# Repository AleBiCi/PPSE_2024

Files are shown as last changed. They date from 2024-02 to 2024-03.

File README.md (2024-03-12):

# PPSE_2024 - SunScanner
Questa repository contiene i file di progetto per l'attività di laboratorio del corso di **Progettazione e Prototipazione di Sistemi Elettronici**.\
Il nostro team ha sviluppato un sistema, denominato **SunScanner**, che tramite dati di geolocalizzazione e lettura della tensione riesce a orientare un pannello fotovoltaico verso il sole con un buon livello di precisione.\
Di seguito vengono elencati i contenuti della repo:
* Nella cartella `SW` è contenuto il progetto PlatformIO per la programmazione della scheda;
* Nella cartella `HW` sono presenti tutti i modelli 3D sviluppati per questo progetto (ed eventualmente pronti per la stampa);
* Nella `DOCUMENTAZIONE` si trova tutto il materiale informativo/le informazioni tecniche utilizzate, compresa la relazione finale.

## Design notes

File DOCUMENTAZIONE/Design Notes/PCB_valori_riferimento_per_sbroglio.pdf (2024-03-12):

Serigrafia

Ref. Componenti -> Tratto 0.16/0.20mm Lettere 0.9/1mm

Descrizioni -> Tratto 0.25 Lettere 1.25mm

Piste rame

Segnale -> 0.2 (minimo 0.127)

Alimentazione 0.5 / 0.75mm

Via

Segnale diametro 0.5mm foro 0.3mm

Alimentazione diametro 1.2mm foro 0.6mm O anche meno

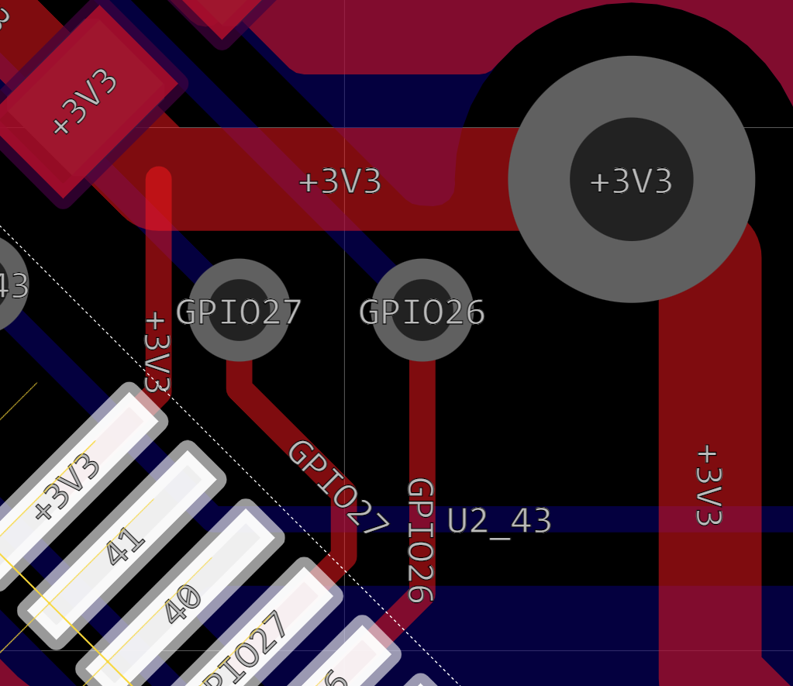
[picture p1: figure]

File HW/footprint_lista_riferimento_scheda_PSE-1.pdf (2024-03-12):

Value | Footprint | Note
Buzzer | Buzzer_Beeper:Buzzer_12x9.5RM7.6
100n | Capacitor_SMD:C_0603_1608Metric
2.2u | Capacitor_SMD:C_0603_1608Metric
18p | Capacitor_SMD:C_0603_1608Metric
4.7u | Capacitor_SMD:C_0603_1608Metric
10u | Capacitor_SMD:C_0805_2012Metric
1u | Capacitor_SMD:C_0603_1608Metric
22u | Capacitor_SMD:C_0805_2012Metric
4u7 | Capacitor_SMD:C_0603_1608Metric
1u 6V3 | Capacitor_SMD:C_0603_1608Metric
WS2812B | LED_SMD:LED_WS2812B_PLCC4_5.0x5.0mm_P3.2mm
1N4148 | Diode_SMD:D_SOD-123
LED_alive | LED_SMD:LED_0603_1608Metric
TVS VBR 17V IBR=1mA | Diode_SMD:D_SMA
S1B | Diode_SMD:D_SMA
RBR1VWM30ATFTR | Diode_SMD:D_SOD-123
3V3_LED | LED_SMD:LED_0805_2012Metric
PDZ3.3B.115 | Diode_SMD:D_SOD-323_HandSoldering
5V_LED | LED_SMD:LED_0805_2012Metric
2016L05MR | Fuse:Fuse_1206_3216Metric
FerriteBead | Capacitor_SMD:C_0805_2012Metric
MountingHole | MountingHole:MountingHole_3.2mm_M3_Pad_Via
WS2812B | Connector_JST:JST_XH_B3B-XH-A_1x03_P2.50mm_Vertical
Conn_01x03 | Connector_PinHeader_2.54mm:PinHeader_1x03_P2.54mm_Vertical
Vin | TerminalBlock:TerminalBlock_bornier-2_P5.08mm
USB_B_Mini | Connector_USB:USB_Mini-B_Wuerth_65100516121_Horizontal
Vout 5V | TerminalBlock:TerminalBlock_bornier-2_P5.08mm
I2C_3V3 | Connector_JST:JST_XH_B4B-XH-A_1x04_P2.50mm_Vertical
UART0_3V3 | Connector_JST:JST_XH_B4B-XH-A_1x04_P2.50mm_Vertical
IRLML0060TRPBF | Package_TO_SOT_SMD:SOT-23
PDTC114YT | Package_TO_SOT_SMD:SOT-23
IRLML9301 | Package_TO_SOT_SMD:SOT-23
1k | Resistor_SMD:R_0603_1608Metric
100k | Resistor_SMD:R_0603_1608Metric
10K | Resistor_SMD:R_0603_1608Metric
10k | Resistor_SMD:R_0603_1608Metric
470k | Resistor_SMD:R_0603_1608Metric
470 | Resistor_SMD:R_0603_1608Metric
27 | Resistor_SMD:R_0603_1608Metric
510 | Resistor_SMD:R_0603_1608Metric
1.8k | Resistor_SMD:R_0603_1608Metric
200 | Resistor_SMD:R_0603_1608Metric
150k | Resistor_SMD:R_0603_1608Metric
56k | Resistor_SMD:R_0603_1608Metric
4.7k | Resistor_SMD:R_0603_1608Metric
47k | Resistor_SMD:R_0603_1608Metric
RESET_SW | Button_Switch_SMD:SW_SPST_EVQP0
PROG_SW | Button_Switch_SMD:SW_SPST_EVQP0
SW_U | Button_Switch_SMD:SW_SPST_EVQP0
SW_L | Button_Switch_SMD:SW_SPST_EVQP0
SW_R | Button_Switch_SMD:SW_SPST_EVQP0
SW_D | Button_Switch_SMD:SW_SPST_EVQP0
Power_button | Button_Switch_SMD:SW_SPST_EVQP0
VBUS | TestPoint:TestPoint_THTPad_D1.5mm_Drill0.7mm
5V | TestPoint:TestPoint_THTPad_D1.5mm_Drill0.7mm
3V3 | TestPoint:TestPoint_THTPad_D1.5mm_Drill0.7mm
3V3A | TestPoint:TestPoint_THTPad_D1.5mm_Drill0.7mm
RP2040 | DA REALIZZARE | Verificare online se esistono footprint di partenza o già disponibili
W25Q16JVUSSQ | DA REALIZZARE | Verificare online se esistono footprint di partenza o già disponibili
AT24C256 | Package_SO:SOIC-8_3.9x4.9mm_P1.27mm
oled_0.96"_128x64px | Connector_PinHeader_2,54mm:PinHeader_1x04_P2.54mm_Vertical | Tenere conto dell'ingombro reale del componente
XC6705A331MR-G | Package_TO_SOT_SMD:SOT-23-5
TPS563201 | Package_TO_SOT_SMD:SOT-23-6
SAM-M8Q | DA REALIZZARE | Verificare online se esistono footprint di partenza o già disponibili
MMA8451Q | DA REALIZZARE | Verificare online se esistono footprint di partenza o già disponibili
ESP-01 | Connector_PinSocket_2,54mm:PinSocket_2x04_P2.54mm_Vertical | Tenere conto dell'ingombro reale del componente
TC1047A | Package_TO_SOT_SMD:SOT-23
12MHz | Crystal:Crystal_SMD_3225-4Pin_3.2x2.5mm_HandSoldering
Induttore 2,2uH | Inductor_SMD:L_Vishay_IHLP-1212 | IHLP1212BZER2R2M11

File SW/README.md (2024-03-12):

## Nota Importante
È possibile aprire e visualizzare correttamente il progetto (completo di dipendenze) solamente utilizzando **PlatformIO**.\
Se si fosse interessati solamente ai file sorgente, nella cartella `src` si trovano i file `.cpp` mentre nella cartella `include` gli header.

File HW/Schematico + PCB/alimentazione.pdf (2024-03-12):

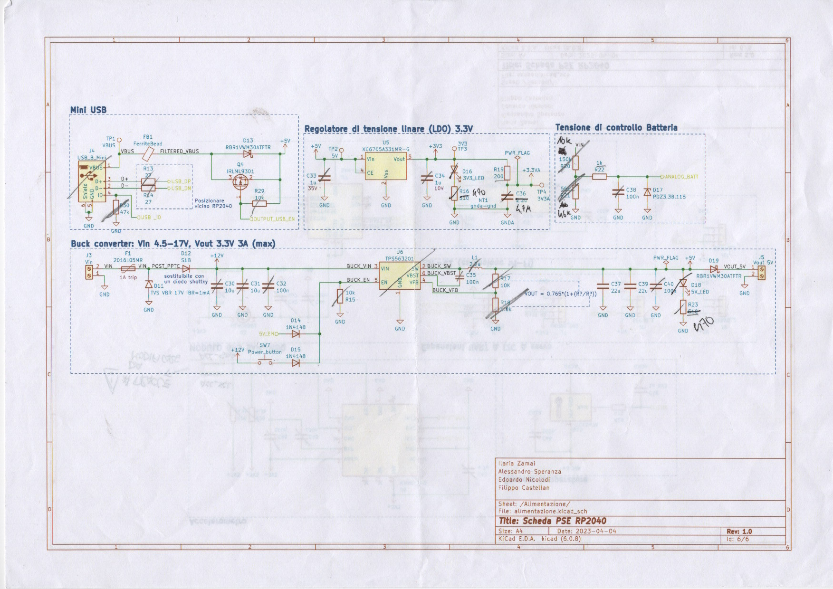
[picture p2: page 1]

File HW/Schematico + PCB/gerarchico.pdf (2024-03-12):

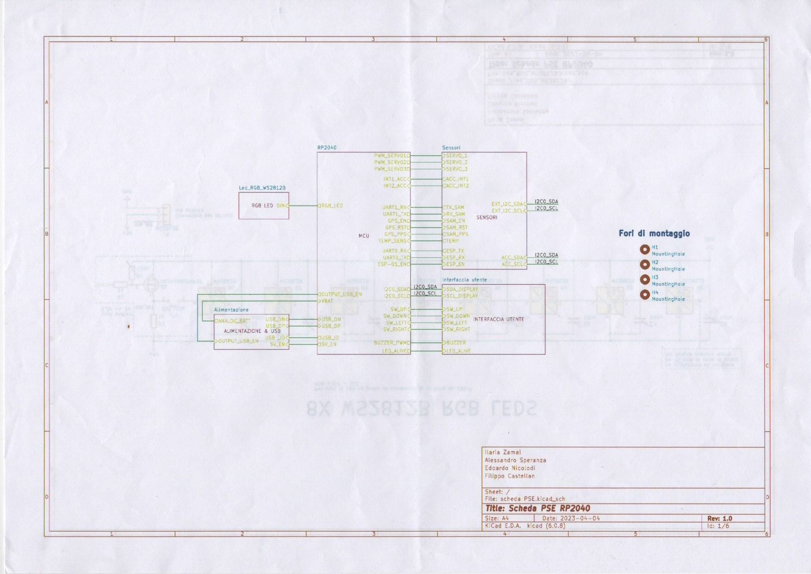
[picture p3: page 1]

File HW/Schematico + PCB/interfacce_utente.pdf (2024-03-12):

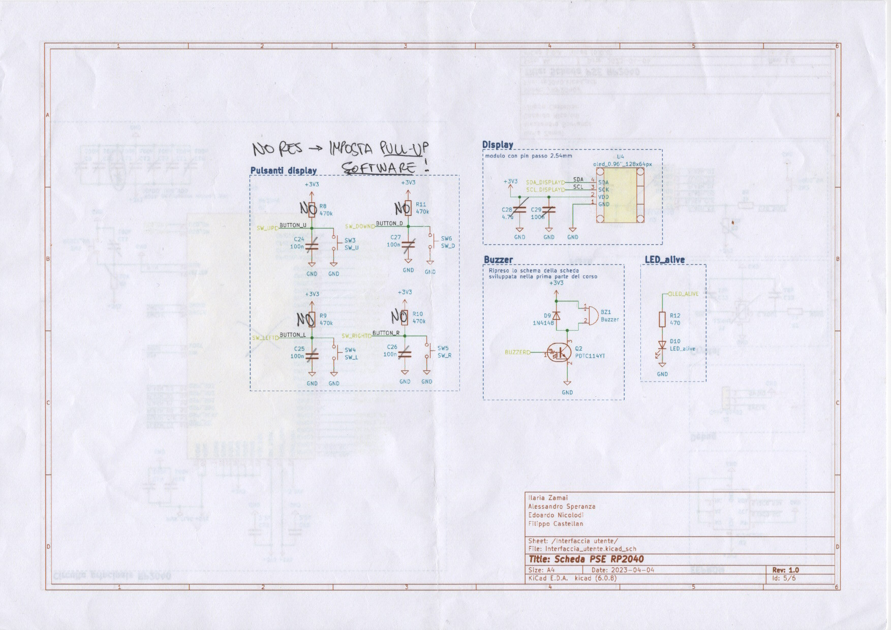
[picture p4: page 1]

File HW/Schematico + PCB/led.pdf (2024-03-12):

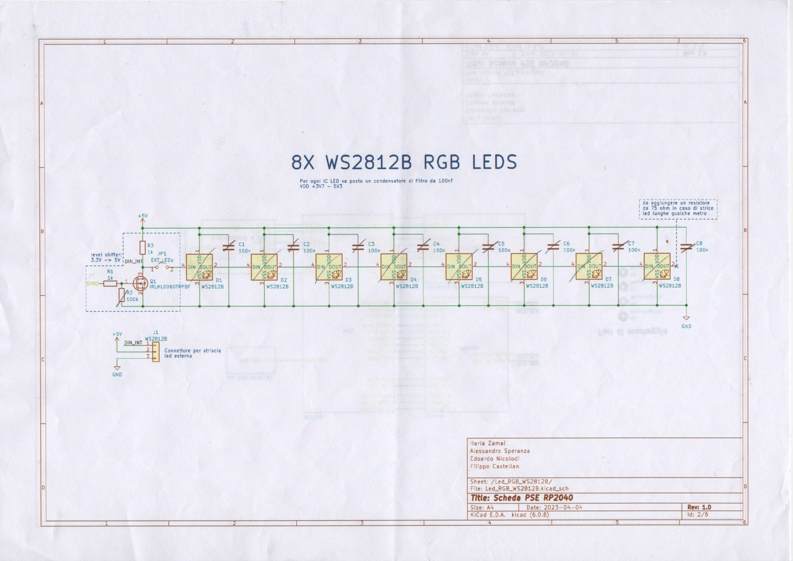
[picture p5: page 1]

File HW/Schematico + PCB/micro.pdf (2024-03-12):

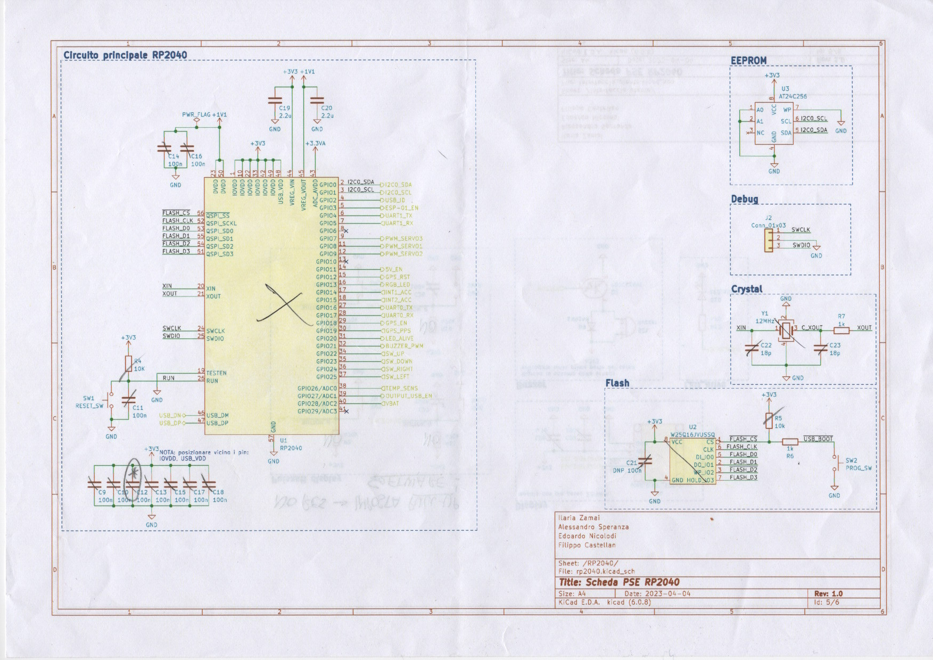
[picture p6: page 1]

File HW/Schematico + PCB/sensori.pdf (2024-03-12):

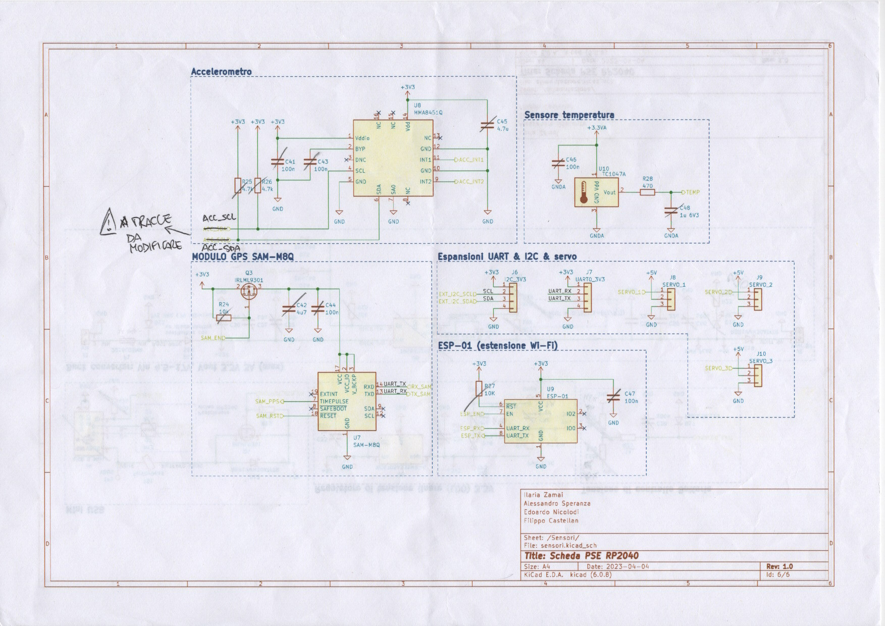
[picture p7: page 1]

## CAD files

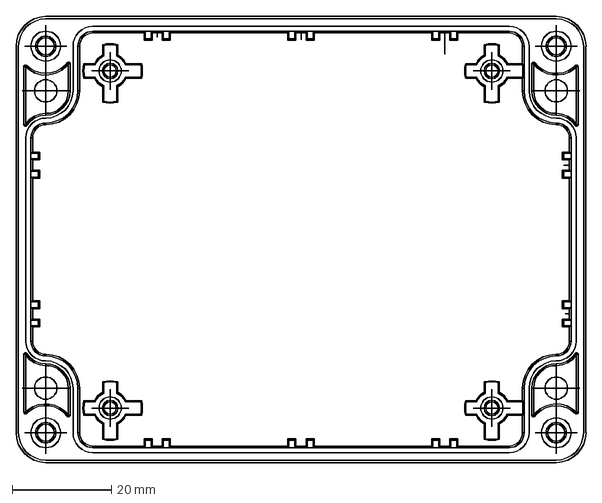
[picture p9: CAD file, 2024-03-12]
DOCUMENTAZIONE/Datasheet/Involucro/involucro_misure.dxf
115.0 x 90.0 mm

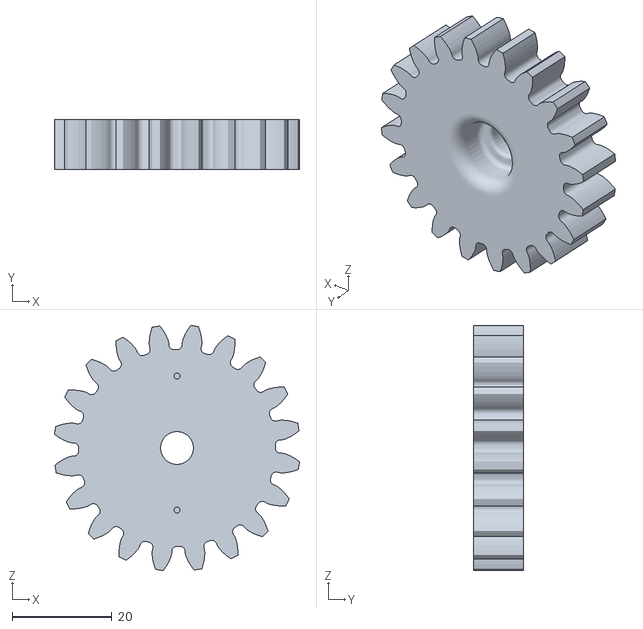
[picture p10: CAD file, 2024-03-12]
HW/Modelli 3D Struttura/ruota_dentata_20_denti.stl
49.2 x 10.0 x 49.2

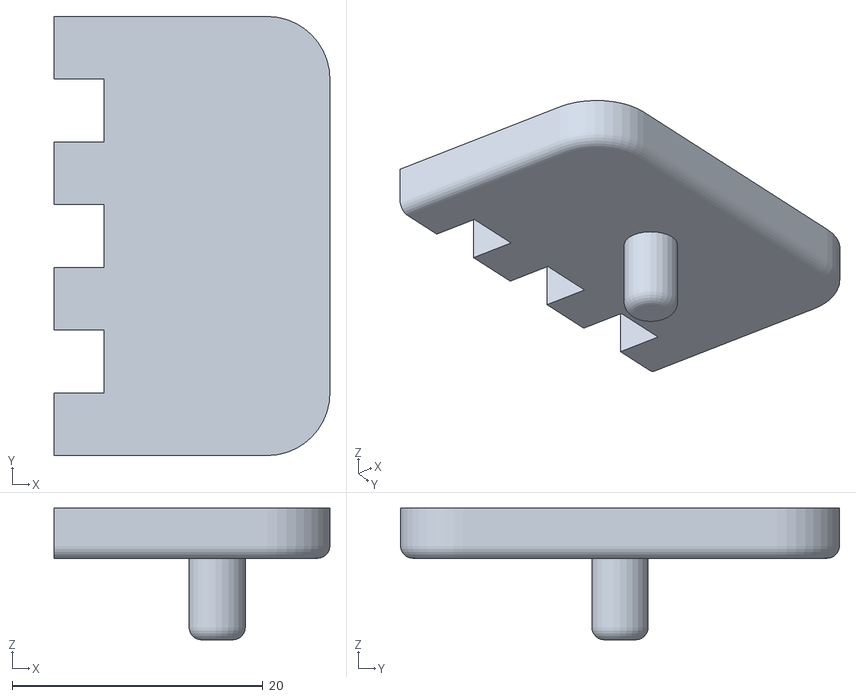
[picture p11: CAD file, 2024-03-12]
HW/Modelli 3D Struttura/top_appoggio.stl
22.0 x 35.0 x 10.5

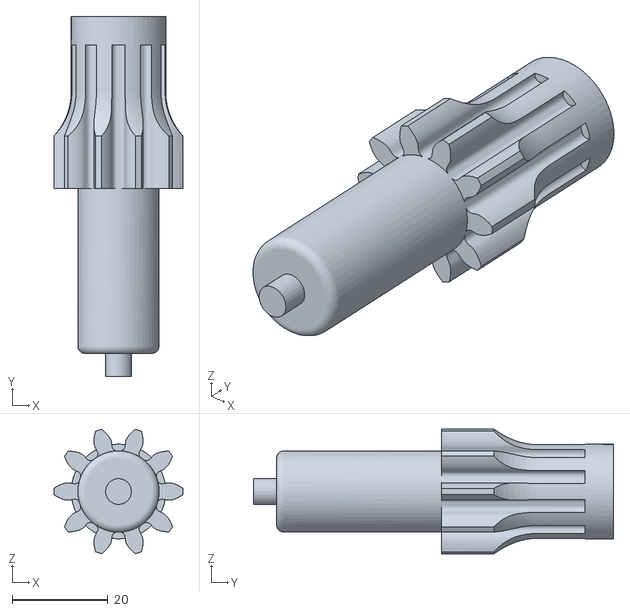
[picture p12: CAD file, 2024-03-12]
HW/Modelli 3D Struttura/asse_primario.stl
27.0 x 75.4 x 26.1

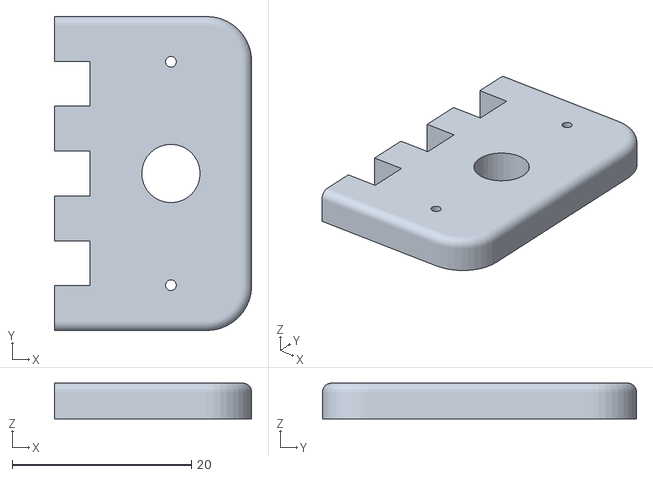
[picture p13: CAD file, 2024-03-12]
HW/Modelli 3D Struttura/top_laterale_perno.stl
22.0 x 35.0 x 4.00

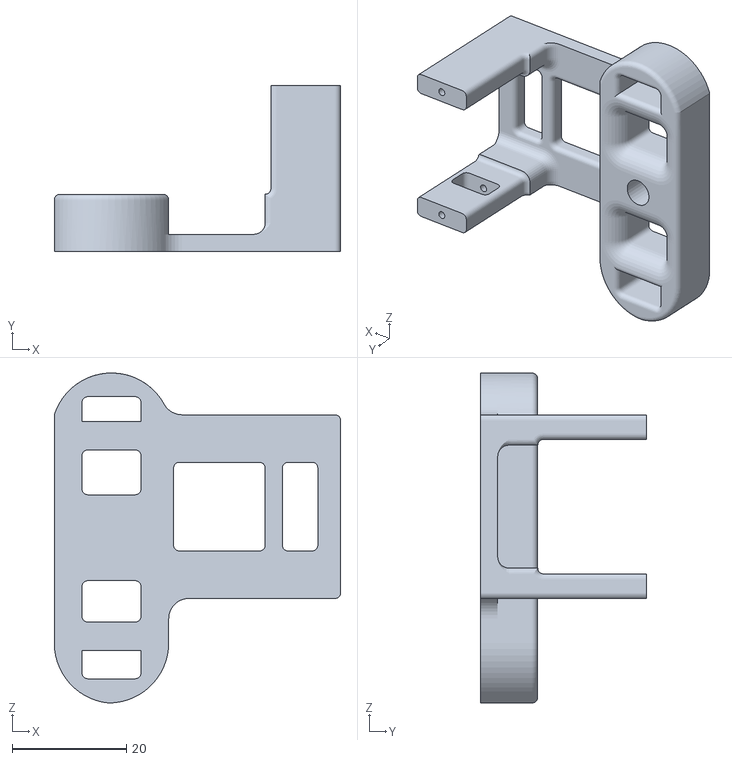
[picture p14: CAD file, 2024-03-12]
HW/Modelli 3D Struttura/base.stl
50.1 x 29.0 x 57.7

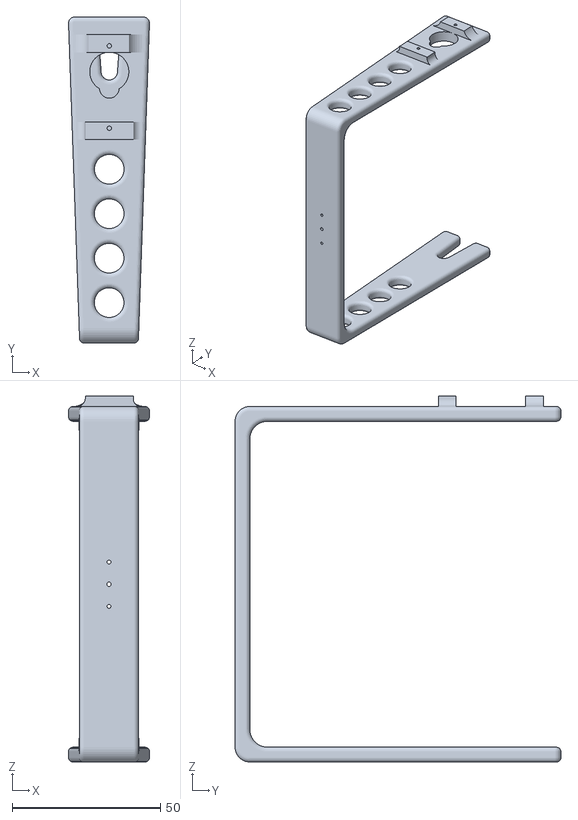
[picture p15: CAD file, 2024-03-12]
HW/Modelli 3D Struttura/braccio.stl
27.3 x 110.0 x 123.5

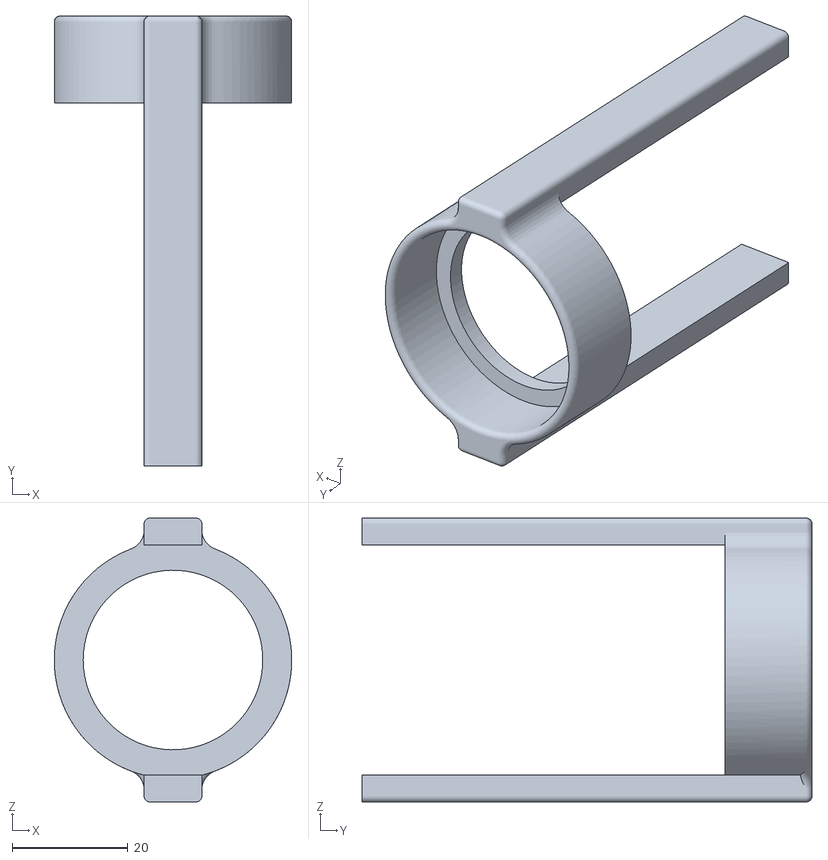
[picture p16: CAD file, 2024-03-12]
HW/Modelli 3D Struttura/reggi_asse_primario.stl
41.0 x 77.7 x 49.0

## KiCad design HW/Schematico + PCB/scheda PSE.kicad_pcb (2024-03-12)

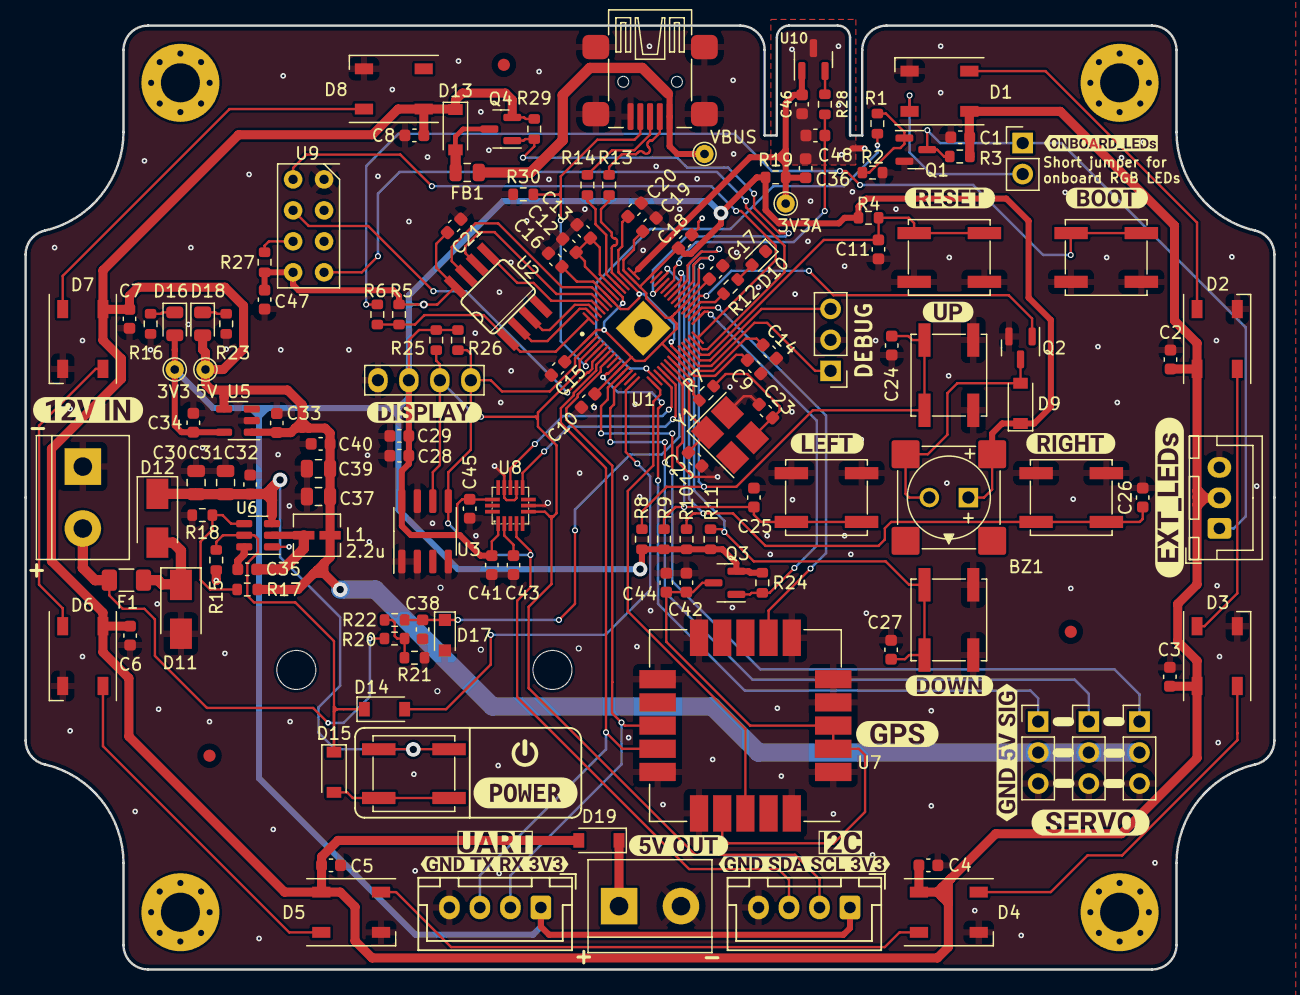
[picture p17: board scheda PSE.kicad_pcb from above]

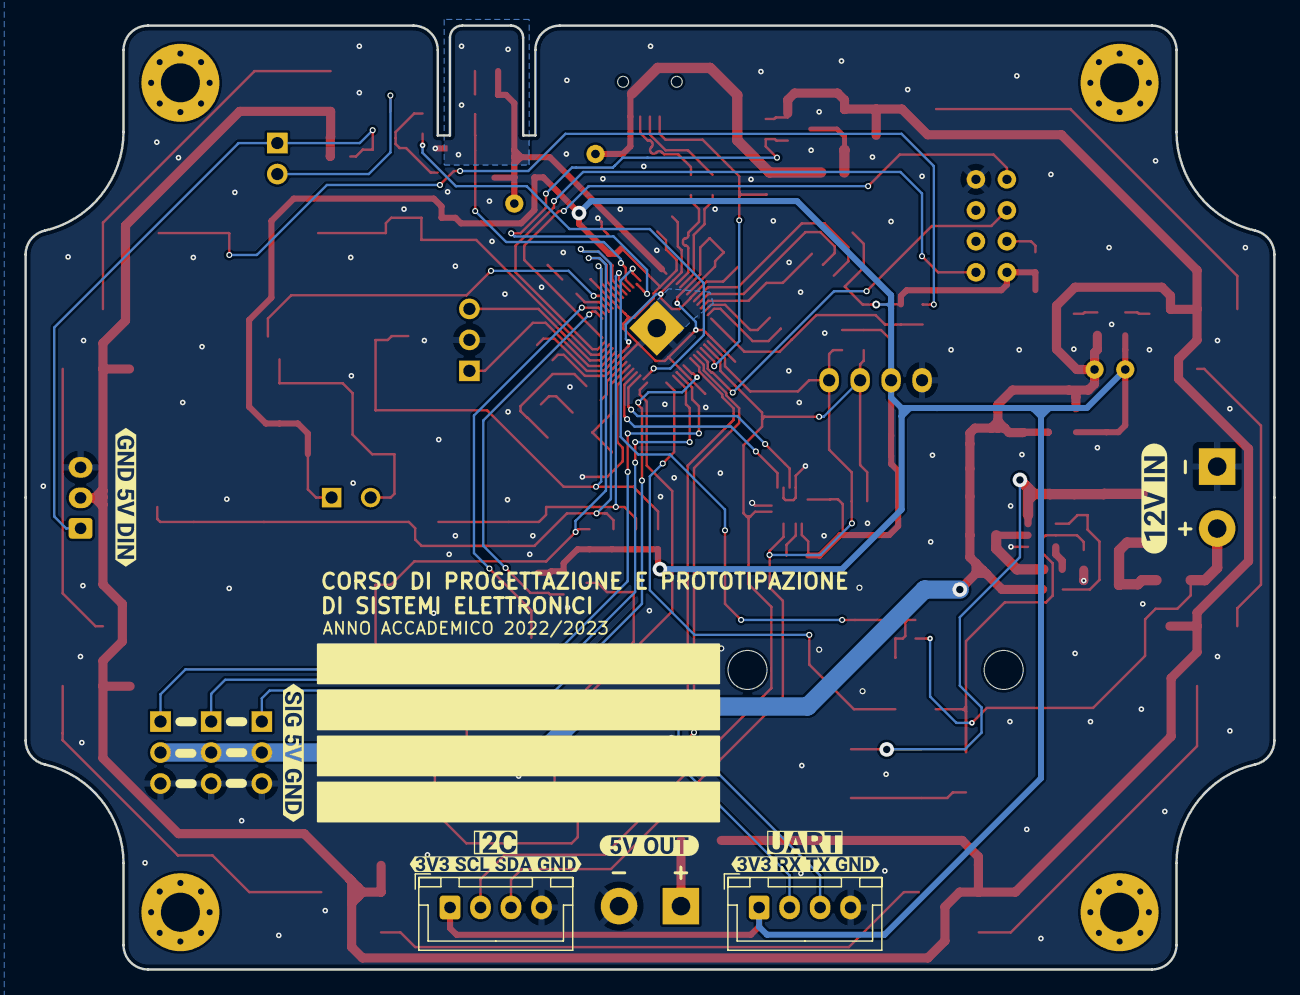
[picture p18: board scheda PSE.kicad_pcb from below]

Board: 2 copper layers, 102.4 x 77.4 mm, 170 parts (10 on the bottom side), 80 nets.

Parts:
BZ1: Buzzer; MLT-8530
C1, C2, C3, C4, C5, C6, C7, C8, C9, C10, C11, C12, C13, C14, C15, C16, C17, C18, C24, C25, C26, C27, C29, C32, C35, C38, C40, C41, C43, C44, C46, C47: 100n; C_0603_1608Metric
C19, C20, C36: 2.2u; C_0603_1608Metric
C21: DNP 100n; C_0603_1608Metric
C22, C23: 18p; C_0603_1608Metric
C28, C45: 4.7u; C_0603_1608Metric
C30, C31: 10u; C_0805_2012Metric
C33, C34: 1u; C_0603_1608Metric
C37, C39: 22u; C_0805_2012Metric
C42: 4u7; C_0603_1608Metric
C48: 1u 6V3; C_0603_1608Metric
D1, D2, D3, D4, D5, D6, D7, D8: WS2812B; LED_WS2812B_PLCC4_5.0x5.0mm_P3.2mm
D9, D14, D15: 1N4148; D_SOD-123
D10: LED_alive; LED_0603_1608Metric
D11: TVS VBR 17V IBR=1mA; D_SMA
D12: S1B; D_SMA
D13, D19: RBR1VWM30ATFTR; D_SOD-123
D16: 3V3_LED; LED_0805_2012Metric
D17: PDZ3.3B.115; D_SOD-323_HandSoldering
D18: 5V_LED; LED_0805_2012Metric
F1: 2016L05MR; Fuse_1206_3216Metric
FB1: FerriteBead; C_0805_2012Metric
H1, H2, H3, H4: MountingHole; MountingHole_3.2mm_M3_Pad_Via
J1: WS2812B; JST_XH_B3B-XH-A_1x03_P2.50mm_Vertical
J2: Conn_01x03; PinHeader_1x03_P2.54mm_Vertical
J3: Vin; TerminalBlock_bornier-2_P5.08mm
J4: USB_B_Mini; USB mini
J5: Vout 5V; TerminalBlock_bornier-2_P5.08mm
J6: I2C_3V3; JST_XH_B4B-XH-A_1x04_P2.50mm_Vertical
J7: UART0_3V3; JST_XH_B4B-XH-A_1x04_P2.50mm_Vertical
J8: SERVO_1; PinHeader_1x03_P2.54mm_Vertical
J9: SERVO_2; PinHeader_1x03_P2.54mm_Vertical
J10: SERVO_3; PinHeader_1x03_P2.54mm_Vertical
JP1: EXT_LEDs; PinHeader_1x02_P2.54mm_Vertical
L1: 2.2u; IHLP1212BZER2R2M11
NT1: gnda-gnd; NetTie-2_SMD_Pad0.5mm
Q1: IRLML0060TRPBF; SOT-23
Q2: PDTC114YT; SOT-23
Q3, Q4: IRLML9301; SOT-23
R1, R3, R6, R7, R22: 1k; R_0603_1608Metric
R2: 100k; R_0603_1608Metric
R4, R17, R27: 10K; R_0603_1608Metric
R5, R15, R24, R29: 10k; R_0603_1608Metric
R8, R9, R10, R11: 470k; R_0603_1608Metric
R12, R28: 470; R_0603_1608Metric
R13, R14: 27; R_0603_1608Metric
R16, R23: 510; R_0603_1608Metric
R18: 1.8k; R_0603_1608Metric
R19: 200; R_0603_1608Metric
R20: 150k; R_0603_1608Metric
R21: 56k; R_0603_1608Metric
R25, R26: 4.7k; R_0603_1608Metric
R30: 47k; R_0603_1608Metric
SW1: RESET_SW; SW_SPST_EVQP0
SW2: PROG_SW; SW_SPST_EVQP0
SW3: SW_U; SW_SPST_EVQP0
SW4: SW_L; SW_SPST_EVQP0
SW5: SW_R; SW_SPST_EVQP0
SW6: SW_D; SW_SPST_EVQP0
SW7: Power_button; SW_SPST_EVQP0
TP1: VBUS; TestPoint_THTPad_D1.5mm_Drill0.7mm
TP2: 5V; TestPoint_THTPad_D1.5mm_Drill0.7mm
TP3: 3V3; TestPoint_THTPad_D1.5mm_Drill0.7mm
TP4: 3V3A; TestPoint_THTPad_D1.5mm_Drill0.7mm
U1: RP2040; QFN40P700X700X90-57N-D
U2: W25Q16JVUSSQ; SOIC8-150mils
U3: AT24C256; SOIC-8_3.9x4.9mm_P1.27mm
U4: oled_0.96"_128x64px; 128x64OLED
U5: XC6705A331MR-G; SOT-23-5
U6: TPS563201; SOT-23-6
U7: SAM-M8Q; SAM_M8Q
U8: MMA8451Q; QFN-16
U9: ESP-01
U10: TC1047A; SOT-23
Y1: 12MHz; Crystal_SMD_3225-4Pin_3.2x2.5mm_HandSoldering
kibuzzard-643CF7B7, kibuzzard-643CF7B7#2: G***; kibuzzard-643CF7B7
kibuzzard-643CF7E4: G***; kibuzzard-643CF7E4
kibuzzard-643CF8F2: G***; kibuzzard-643CF8F2
kibuzzard-643CF9A0: G***; kibuzzard-643CF9A0
kibuzzard-643CF9B2: G***; kibuzzard-643CF9B2
kibuzzard-643CF9C9: G***; kibuzzard-643CF9C9
kibuzzard-643CF80B, kibuzzard-643CF80B#2: G***; kibuzzard-643CF80B
kibuzzard-643CF88B: G***; kibuzzard-643CF88B
kibuzzard-643CF96E: G***; kibuzzard-643CF96E
kibuzzard-643CF430: G***; kibuzzard-643CF430
kibuzzard-643CF710: G***; kibuzzard-643CF710
kibuzzard-643CF960: G***; kibuzzard-643CF960
kibuzzard-643CF993: G***; kibuzzard-643CF993
kibuzzard-643CFA52, kibuzzard-643CFA52#2: G***; kibuzzard-643CFA52
kibuzzard-643CFABC, kibuzzard-643CFABC#2: G***; kibuzzard-643CFABC
kibuzzard-643CFBDA: G***; kibuzzard-643CFBDA
kibuzzard-643D3A9E: G***; kibuzzard-643D3A9E
kibuzzard-643DAACA: G***; kibuzzard-643DAACA
kibuzzard-643E45C8: G***; kibuzzard-643E45C8
kibuzzard-643E45D3: G***; kibuzzard-643E45D3
kibuzzard-643E4714: G***; kibuzzard-643E4714
kibuzzard-643E4784: G***; kibuzzard-643E4784
kibuzzard-644128D0: G***; kibuzzard-644128D0

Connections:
+1V1: C14.1, C16.1, C20.1, U1.23 (DVDD), U1.45 (VREG_VOUT), U1.50 (DVDD)
+3.3VA: C36.1, C46.1, R19.2, TP4.1, U1.43 (ADC_AVDD), U10.1 (Vdd)
+3V3: BZ1.1 (-), C9.1, C10.1, C12.1, C13.1, C15.1, C17.1, C18.1, C19.1, C21.1, C28.1, C29.1, C34.1, C41.1, C45.1, C47.1, D9.1 (K), D16.2 (A), J6.1, J7.1, Q3.2 (S), R4.1, R5.1, R8.1, R9.1, R10.1, R11.1, R19.1, R24.1, R25.1, R26.1, R27.1, TP3.1, U1.1 (IOVDD), U1.10 (IOVDD), U1.22 (IOVDD), U1.33 (IOVDD), U1.42 (IOVDD), U1.44 (VREG_VIN), U1.48 (USB_VDD), U1.49 (IOVDD), U2.8 (VCC), U3.8 (VCC), U4.2 (VDD), U5.5 (Vout), U8.1 (Vddio), U8.14 (Vdd), U9.5 (VCC)
+5V: C1.1, C2.1, C3.1, C4.1, C5.1, C6.1, C7.1, C8.1, C33.1, C37.1, C39.1, C40.1, D1.1 (VDD), D2.1 (VDD), D3.1 (VDD), D4.1 (VDD), D5.1 (VDD), D6.1 (VDD), D7.1 (VDD), D8.1 (VDD), D13.1 (K), D18.2 (A), D19.2 (A), J1.2, J8.2, J9.2, J10.2, L1.2, Q4.2 (S), R3.2, R17.1, R29.2, TP2.1, U5.1 (Vin), U5.4 (CE)
+12V: C30.1, C31.1, C32.1, D12.1 (K), SW7.1, U6.3 (VIN)
/Alimentazione/5V_EN: D14.2 (A), U1.14 (GPIO11)
/Alimentazione/ANALOG_BATT: C38.1, D17.1 (K), R22.1, U1.40 (GPIO28/ADC2)
/Alimentazione/BUCK_EN: D14.1 (K), D15.1 (K), R15.1, U6.5 (EN)
/Alimentazione/BUCK_SW: C35.1, L1.1, U6.2 (SW)
/Alimentazione/BUCK_VBST: C35.2, U6.6 (VBST)
/Alimentazione/BUCK_VFB: R17.2, R18.1, U6.4 (VFB)
/Alimentazione/D+: J4.3 (D+), R13.1
/Alimentazione/D-: J4.2 (D-), R14.2
/Alimentazione/FILTERED_VBUS: D13.2 (A), FB1.2, Q4.3 (D)
/Alimentazione/OUTPUT_USB_EN: Q4.1 (G), R29.1, U1.39 (GPIO27/ADC1)
/Alimentazione/USB _ID: J4.4 (ID), R30.1, U1.4 (GPIO2)
/Alimentazione/USB_DN: R14.1, U1.46 (USB_DM)
/Alimentazione/USB_DP: R13.2, U1.47 (USB_DP)
/Alimentazione/VBUS: FB1.1, J4.1 (VBUS), TP1.1
/Alimentazione/VIN: F1.1, J3.2, R20.1
/Alimentazione/VIN_ POST_PPTC: D11.1 (A1), D12.2 (A), F1.2
/Alimentazione/VOUT_5V: D19.1 (K), J5.1
/I2C0_SCL: J6.2, R25.2, U1.3 (GPIO1), U3.6 (SCL), U4.3 (SCK), U8.6 (SDA)
/I2C0_SDA: J6.3, R26.2, U1.2 (GPIO0), U3.5 (SDA), U4.4 (SDA), U8.4 (SCL)
/Interfaccia utente/BUTTON_D: C27.1, R11.2, SW6.1, U1.35 (GPIO23)
/Interfaccia utente/BUTTON_L: C25.1, R9.2, SW4.2, U1.37 (GPIO25)
/Interfaccia utente/BUTTON_R: C26.1, R10.2, SW5.2, U1.36 (GPIO24)
/Interfaccia utente/BUTTON_U: C24.1, R8.2, SW3.2, U1.34 (GPIO22)
/Interfaccia utente/BUZZER: Q2.1 (B), U1.32 (GPIO21)
/Interfaccia utente/LED_ALIVE: R12.1, U1.31 (GPIO20)
/Led_RGB_WS2812B/DIN: R1.1, U1.16 (GPIO13)
/Led_RGB_WS2812B/DIN_INT: J1.1, JP1.1 (A), Q1.3 (D), R3.1
/RP2040/C_XOUT: C23.1, R7.1, Y1.3
/RP2040/ESP-01_EN: U1.5 (GPIO3), U9.7 (EN)
/RP2040/FLASH_CLK: U1.52 (QSPI_SCKL), U2.6 (CLK)
/RP2040/FLASH_D0: U1.53 (QSPI_SD0), U2.5 (DI_IO0)
/RP2040/FLASH_D1: U1.55 (QSPI_SD1), U2.2 (DO_IO1)
/RP2040/FLASH_D3: U1.51 (QSPI_SD3), U2.7 (HOLD_IO3)
/RP2040/GPS_EN: Q3.1 (G), R24.2, U1.29 (GPIO18)
/RP2040/GPS_PPS: U1.30 (GPIO19), U7.7 (TIMEPULSE)
/RP2040/GPS_RST: U1.15 (GPIO12), U7.18 (~RESET)
/RP2040/INT1_ACC: U1.17 (GPIO14), U8.11 (INT1)
/RP2040/INT2_ACC: U1.18 (GPIO15), U8.9 (INT2)
/RP2040/PWM_SERVO1: J8.1, U1.11 (GPIO8)
/RP2040/PWM_SERVO2: J9.1, U1.12 (GPIO9)
/RP2040/PWM_SERVO3: J10.1, U1.9 (GPIO7)
/RP2040/RUN: C11.1, R4.2, SW1.2, U1.26 (RUN)
/RP2040/SWCLK: J2.1, U1.24 (SWCLK)
/RP2040/SWDIO: J2.3, U1.25 (SWDIO)
/RP2040/TEMP_SENS: C48.1, R28.2, U1.38 (GPIO26/ADC0)
/RP2040/UART0_RX: U1.28 (GPIO17), U9.8 (UART_TX)
/RP2040/UART0_TX: U1.27 (GPIO16), U9.4 (UART_RX)
/RP2040/XIN: C22.1, U1.20 (XIN), Y1.1
/RP2040/XOUT: R7.2, U1.21 (XOUT)
/RP2040/~FLASH_CS: R5.2, R6.2, U1.56 (~QSPI_SS), U2.1 (~CS)
/RP2040/~FLASH_D2: U1.54 (QSPI_SD2), U2.3 (WP_IO2)
/RP2040/~USB_BOOT: R6.1, SW2.1
/Sensori/UART_RX: J7.2, U1.7 (GPIO5), U7.13 (TXD)
/Sensori/UART_TX: J7.3, U1.6 (GPIO4), U7.14 (RXD)
GND: C1.2, C2.2, C3.2, C4.2, C5.2, C6.2, C7.2, C8.2, C9.2, C10.2, C11.2, C12.2, C13.2, C14.2, C15.2, C16.2, C17.2, C18.2, C19.2, C20.2, C21.2, C22.2, C23.2, C24.2, C25.2, C26.2, C27.2, C28.2, C29.2, C30.2, C31.2, C32.2, C33.2, C34.2, C37.2, C38.2, C39.2, C40.2, C41.2, C42.2, C43.2, C44.2, C45.2, C47.2, D1.3 (VSS), D2.3 (VSS), D3.3 (VSS), D4.3 (VSS), D5.3 (VSS), D6.3 (VSS), D7.3 (VSS), D8.3 (VSS), D10.1 (K), D11.2 (A2), D17.2 (A), J1.3, J2.2, J3.1, J4.5 (GND), J4.6 (Shield), J5.2, J6.4, J7.4, J8.3, J9.3, J10.3, NT1.1, Q1.2 (S), Q2.2 (E), R2.1, R15.2, R16.2, R18.2, R21.2, R23.2, R30.2, SW1.1, SW2.2, SW3.1, SW4.1, SW5.1, SW6.2, U1.19 (TESTEN), U1.57 (GND), U2.4 (GND), U3.1 (A0), U3.2 (A1), U3.4 (GND), U3.7 (WP), U4.1 (GND), U5.2 (Vss), U6.1 (GND), U7.1 (GND), U7.4 (GND), U7.5 (GND), U7.6 (GND), U7.10 (GND), U7.11 (GND), U7.15 (GND), U7.16 (GND), U7.20 (GND), U8.5 (GND), U8.7 (SA0), U8.10 (GND), U8.12 (GND), U9.1 (GND), Y1.2, Y1.4
GNDA: C36.2, C46.2, C48.2, NT1.2, U10.3 (GND)
unnamed: BZ1.2 (+), D9.2 (A), Q2.3 (C)
unnamed: C42.1, C44.1, Q3.3 (D), U7.2 (VCC_IO), U7.3 (V_BCKP), U7.17 (VCC)
unnamed: C43.1, U8.2 (BYP)
unnamed: D1.2 (DOUT), D2.4 (DIN)
unnamed: D1.4 (DIN), JP1.2 (B)
unnamed: D2.2 (DOUT), D3.4 (DIN)
unnamed: D3.2 (DOUT), D4.4 (DIN)
unnamed: D4.2 (DOUT), D5.4 (DIN)
unnamed: D5.2 (DOUT), D6.4 (DIN)
unnamed: D6.2 (DOUT), D7.4 (DIN)
unnamed: D7.2 (DOUT), D8.4 (DIN)
unnamed: D10.2 (A), R12.2
unnamed: D15.2 (A), SW7.2
unnamed: D16.1 (K), R16.1
unnamed: D18.1 (K), R23.1
unnamed: Q1.1 (G), R1.2, R2.2
unnamed: R20.2, R21.1, R22.2
unnamed: R27.2, U9.6 (~RST)
unnamed: R28.1, U10.2 (Vout)

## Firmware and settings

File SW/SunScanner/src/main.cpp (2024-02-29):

#include "servoLib/servo_control.h" //Libreria servo
#include "oled/menu.h"  //Libreria display
#include "gps/NMEAParser.h"  //Libreria set-up e parsing gps
#include "led/led.h"  //Libreria per controllo LED
#include <Arduino.h>
#include <QMC5883LCompass.h>  //Libreria controllo bussola
#include <string>
// #include <Adafruit_NeoPixel.h>
#include <NeoPixelConnect.h>

#define BTN_UP 22
#define BTN_DOWN 23
#define BTN_LEFT 25
#define BTN_RIGHT 24

#define PIN_SERVO_AZ 7
#define PIN_SERVO_EL 8

#define PIN_VOLTAGE 29

#define UART1_RX 5
#define UART1_TX 4
#define GPS_nEN 18  // Attenzione: GPS_EN è negato ==> attivo basso
#define UART_BAUDRATE 9600 // Baud rate per comunicazione UART con GPS
#define CHUNK_SIZE 8
#define BUFFER_SIZE 80 // Dimensione massima del buffer UART, corrisponde a massima lunghezza di una frase NMEA

// Messaggi per la configurazione del SAM-M8Q
uint8_t UBX_CFG_MSG_GGA_OFF[] = {                   // UBX-CFG-MSG NMEA-GGA Off on All interfaces
    0xB5, 0x62, 0x06, 0x01, 0x08, 0x00,             // Header
    0xF0, 0x00, 0x00, 0x00, 0x00, 0x00, 0x00, 0x00, // Payload
    0xFF, 0x23};                                    // Checksum

uint8_t UBX_CFG_MSG_GSV_OFF[] = {                   // UBX-CFG-MSG NMEA-GSV Off on All interfaces
    0xB5, 0x62, 0x06, 0x01, 0x08, 0x00,
    0xF0, 0x03, 0x00, 0x00, 0x00, 0x00, 0x00, 0x00,
    0x02, 0x38};  
                                  
uint8_t UBX_CFG_MSG_GSA_OFF[] = {                   // UBX-CFG-MSG NMEA-GSA Off on All interfaces
    0xB5, 0x62, 0x06, 0x01, 0x08, 0x00,
    0xF0, 0x02, 0x00, 0x00, 0x00, 0x00, 0x00, 0x00, 
    0x01, 0x31};                                    

uint8_t UBX_CFG_MSG_VTG_OFF[] = {                   // UBX-CFG-MSG NMEA-VTG Off on All interfaces
    0xB5, 0x62, 0x06, 0x01, 0x08, 0x00,
    0xF0, 0x05, 0x00, 0x00, 0x00, 0x00, 0x00, 0x00, 
    0x04, 0x46};
                                    
uint8_t UBX_CFG_MSG_GLL_OFF[] = {                   // UBX-CFG-MSG NMEA-GLL Off on All interfaces
    0xB5, 0x62, 0x06, 0x01, 0x08, 0x00,
    0xF0, 0x01, 0x00, 0x00, 0x00, 0x00, 0x00, 0x00, 
    0x00, 0x2A};                                    

// Stati della MSF che controlla il flow di esecuzione
typedef enum {
    STATE_ACTIONS,
    STATE_POSITIONING,
    STATE_FINE_POINTING,
    STATE_WAIT_AUTO,
    STATE_ZENIT,
    STATE_MANUAL,
    STATE_WAIT_BACK,
    STATE_GPS_ACQUIRE
}State_t;

/* Tipo che rappresenta uno stato:                                            */
/* state => nome stato                                                        */
/* state_function => puntatore a funzione, cio che viene eseguito nello stato */
typedef struct{
    State_t state;
    void (*state_function)(void);
} StateMachine_t;

/* Funzioni che catturano la pressione di un pulsante */
void btn_up_pressed(void);
void btn_down_pressed(void);
void btn_left_pressed(void);
void btn_right_pressed(void);

/* Funzioni di ogni stato */
void fn_ACTIONS(void);
void fn_POSITIONING(void);
void fn_FINE_POINTING(void);
void fn_WAIT_AUTO(void);
void fn_ZENIT(void);
void fn_MANUAL(void);
void fn_WAIT_BACK(void);
void fn_GPS_ACQUIRE(void);

State_t current_state = STATE_ACTIONS; //stato di partenza

QMC5883LCompass compass;  // variabile per controllo della bussola

ServoController servo_controller(PIN_SERVO_AZ,PIN_SERVO_EL,PIN_VOLTAGE,PIN_VOLTAGE); //variabile per controllo servo

int btn_pressed_id; //variabile per identificare il bottone premuto, 0->none 1->up 2->down 3->left 4->right

int manual_control_mode=0; //variabile per identificare il servo da muovere in modalità manuale, 0->az 1->el

/* menu_dept: spostamenti a dx e sx nel menu               */
/* menu_hight_1: spostamenti su e giu nella prima pagina   */
/* menu_hight_2: spostamenti su e giu nella seconda pagina */
int menu_dept=1, menu_hight_1=2, menu_hight_2=1;

long int attesa_auto_pos;  //variabile che tiene traccia del momento dell'ultimo posizionamento automatico

char read_char;  //variabile che tiene i caratteri letti dal gps

// Buffer per il canale seriale UART (8 bit)
char buffer_uart1[BUFFER_SIZE] = "";

MessageRMC message;  //variabile per lo store del parsing dei dati GPS

std::string sent;

double az_val;  //valore di azimuth del sole
double el_val;  //valore di elevazione del sole

void setupM8Q();  //funzione per inizializzare il gps

int pacMan(int start ,int val, int range);  //funzione per mantenere in range menu_hight_1 e menu_hight_2

/* creazione della macchina a stati */
StateMachine_t fsm[] = {
                      {STATE_ACTIONS, fn_ACTIONS},
                      {STATE_POSITIONING, fn_POSITIONING},
                      {STATE_FINE_POINTING, fn_FINE_POINTING},
                      {STATE_WAIT_AUTO, fn_WAIT_AUTO},
                      {STATE_ZENIT, fn_ZENIT},
                      {STATE_MANUAL, fn_MANUAL},
                      {STATE_GPS_ACQUIRE, fn_GPS_ACQUIRE}
};

/* stato che gestisce la pressione dei bottoni */
void fn_ACTIONS(){
  switch(btn_pressed_id){
    case 1/*UP*/:{
      if(menu_dept == 1){
        menu_hight_1=pacMan(2,--menu_hight_1,3);
        clear_disp();
      }
      if(menu_dept == 2 && menu_hight_1 == 3){
        menu_hight_2=pacMan(1,--menu_hight_2,3);
        clear_disp();
      }
      break;
    }
    case 2/*DOWN*/:{
      if(menu_dept == 1){
        menu_hight_1=pacMan(2,++menu_hight_1,3);
        clear_disp();
      }
      if(menu_dept == 2 && menu_hight_1 == 3){
        menu_hight_2=pacMan(1,++menu_hight_2,3);
        clear_disp();
      }
      break;
    }
    case 3/*LEFT*/:{
      if(menu_dept == 2){
        --menu_dept;
        clear_disp();
      }
      break;
    }
    case 4/*RIGHT*/:{
      if(menu_dept == 2 && menu_hight_1 == 3){
        switch(menu_hight_2){
          case 1:{
            current_state = STATE_GPS_ACQUIRE;
            break;
          }
          case 2:{
            current_state = STATE_ZENIT;
            break;
          }
          case 3:{
            current_state = STATE_MANUAL;
            break;
          }
        }
        ++menu_dept;
        clear_disp();
      }
      if(menu_dept == 1){
        ++menu_dept;
        clear_disp();
      }
      break;
    }
  }
  
  btn_pressed_id = 0;
  delay(100);
}

/* funzione per il posizionamento automatico */
void fn_POSITIONING(void){
  compass.read();
  servo_controller.auto_positioning(&(message.time),message.latitude,message.longitude,400,compass.getAzimuth(),&az_val,&el_val);
 
  /* messaggi seriali di debug */
  Serial.print("el: ");
  Serial.println(el_val);
  Serial.println(message.longitude);
  Serial.println(message.latitude);
    
  current_state = STATE_FINE_POINTING;
  btn_pressed_id == 0;
}

/* stato per aggiustare la posizione dei servo utilizzando la tensione letta */
void fn_FINE_POINTING(void){
  servo_controller.max_power_pos(2,5);  //vengono eseguiti 5 step da 2 gradi per ogni direzione
  attesa_auto_pos=millis();  //viene salvato il tempo dell'ultimo posizionamento
  current_state = STATE_WAIT_AUTO;
  btn_pressed_id == 0;
}

/* stato che attende o il superamento dell'intervallo di tempo per poter rieseguire il */
/* posizionamento automatico o la pressione del bottone sinistro per uscire dalla      */
/* modalità automatica                                                                 */
void fn_WAIT_AUTO(void){
  if(millis()-attesa_auto_pos > 180000){ // passati 3 minuti
    current_state = STATE_GPS_ACQUIRE;
  }
  if(btn_pressed_id == 3){ //pressione tasto sinistro
    --menu_dept;
    clear_disp();
    current_state = STATE_ACTIONS;
  }
  btn_pressed_id = 0;

}

/* Il pannello viene posizionato verticalmente */
void fn_ZENIT(void){
  servo_controller.servoEl.set_servo(90);
  current_state = STATE_ACTIONS;
  --menu_dept;
  clear_disp();
  btn_pressed_id == 0;
}

/* Funzione di controllo manuale */
void fn_MANUAL(void){
  switch(btn_pressed_id){
    case 1/*UP*/:{ //movimento di uno dei servo
      if(manual_control_mode==0){
        servo_controller.servoAz.set_servo(servo_controller.servoAz.get_alpha()+5);
      }else{
        servo_controller.servoEl.set_servo(servo_controller.servoEl.get_alpha()+5);
      }
      break;
    }
    case 2/*DOWN*/:{ //movimento di uno dei servo
      if(manual_control_mode==0){
        servo_controller.servoAz.set_servo(servo_controller.servoAz.get_alpha()-5);
      }else{
        servo_controller.servoEl.set_servo(servo_controller.servoEl.get_alpha()-5);
      }
      break;
    }
    case 3/*LEFT*/:{ //uscita dalla modalita manuale
      menu_dept--;
      clear_disp();
      btn_pressed_id == 0;
      current_state = STATE_ACTIONS;
      break;
    }
    case 4/*RIGHT*/:{ //cambio del servo pilotato
      if(manual_control_mode==0){
        manual_control_mode = 1;
      }else{
        manual_control_mode = 0;
      }
      break;
    }
  }
  btn_pressed_id = 0;
}

/* stato per l'acquisizione e il parsing dei dati gps */
void fn_GPS_ACQUIRE(void) {
  int iterNotFixed = 0;
  int iterFixed = 0;
  int totIter = 0;
  int ledIter = 0;
  bool flag = false;

  while(iterFixed < 10 && iterNotFixed < 20) { // Il ciclo di acquisizione prosegue finché non sono stati ricevuti 10 messaggi fixed o 20 non fixed
    if (Serial2.available())
    {
      read_char = Serial2.read();
      strncat(buffer_uart1, &read_char, 1); // Legge un carattere alla volta dalla seriale e lo inserisce nel buffer_uart1
      if (read_char == '\n') // Se il carattere ricevuto è il terminatore ho acquisito una sentence intera
      {
        if (!flag)
        { // Ignora il contenuto del primo buffer -> potrebbe contenere messaggi GNTXT che romperebbero parseRMC
          flag = true;
          strcpy(buffer_uart1, ""); // Svuota buffer
        }
        else
        {
          sent.assign(buffer_uart1, strlen(buffer_uart1)); // Popolo la stringa sent
          if (parseRMC(sent, message))
          { // GPS non fixato
            singleLedIfFixed(false, totIter); // Un led alla volta lampeggia di arancione
            /* Messaggi per debug */
            Serial.print(sent.data());
            Serial.println("ITER");
            Serial.println(iterNotFixed);

            iterNotFixed++;
          }
          else
          { // GPS fixato
            singleLedIfFixed(true, totIter); // Un led alla volta lampeggia di verde
            /* Messaggi per debug */
            Serial.print(sent.data());
            Serial.println("ITER FIXED");
            Serial.println(iterFixed);

            iterFixed++;
          }
          totIter++;
          strcpy(buffer_uart1, "");
        }
      }
    }
  }

  /* Messaggi per debug */
  Serial.print(message.latitude);
  Serial.println();
  Serial.print(message.longitude);
  Serial.println();
  Serial.print(message.time.tm_hour);
  Serial.println();
  Serial.print(message.time.tm_min);
  Serial.println();
  Serial.print(message.time.tm_sec);
  Serial.println();
  Serial.print(message.time.tm_mday);
  Serial.println();
  Serial.print(message.time.tm_mon);
  Serial.println();
  Serial.print(message.time.tm_year);
  Serial.println();

  if (iterFixed >= 10)
  { // Ricevuti almeno 10 messaggi validi
    for (int i = 0; i < 3; ++i)
    {
      // Tutti i led lampeggiano tre volte di verde
      setAllLedGreen();
      delay(200);
      setLedOff();
      delay(200);
    }
    current_state = STATE_POSITIONING; // Ho acquisito dati buoni, quindi passo al posizionamento dei motori
  }
  else
  {
    for (int i = 0; i < 3; ++i)
    {
      // Tutti i led lampeggiano tre volte di arancione
      setAllLedOrange();
      delay(200);
      setLedOff();
      delay(200);
    }
    attesa_auto_pos = millis();
    current_state = STATE_WAIT_AUTO; // Torno ad aspettare per un intervallo di tempo prefissato prima di riposizionare
  }
}

void btn_up_pressed(void){
  btn_pressed_id = 1;
}
void btn_down_pressed(void){
  btn_pressed_id = 2;
}
void btn_left_pressed(void){
  btn_pressed_id = 3;
}
void btn_right_pressed(void){
  btn_pressed_id = 4;
}


void setup() {
  // Apertura seriale virtuale (USB) a 9600 baud
  Serial.begin(9600);

  /* setup pin I2C */
  Wire.setSDA(0);
  Wire.setSCL(1);

  setup_disp();

  /* Setup gps */
  // Setta i pin 5 e 4 come ricevitore e trasmettitore per UART1 (Possibile che siano già settati di default)
  // Uso Serial2, vedi pinout Raspberry Pi Pico e specifiche seriali della libreria Arduino-pico
  Serial2.setRX(UART1_RX);
  Serial2.setTX(UART1_TX);
  Serial2.begin(UART_BAUDRATE); // UART0 su PICO (RP2040)
  
  // Setup del ricevitore GNSS
  pinMode(GPS_nEN, OUTPUT);
  digitalWrite(GPS_nEN, LOW); // GPS_EN e' attivo basso
  setupM8Q();
  delay(5000);

  /*setup pulsanti*/
  pinMode(BTN_UP,INPUT_PULLUP);
  pinMode(BTN_DOWN,INPUT_PULLUP);
  pinMode(BTN_LEFT,INPUT_PULLUP);
  pinMode(BTN_RIGHT,INPUT_PULLUP);

  /* funzioni per attivare attivare gli interrupt sui pin dei pulsanti */
  attachInterrupt(digitalPinToInterrupt(BTN_UP), btn_up_pressed, FALLING );
  attachInterrupt(digitalPinToInterrupt(BTN_DOWN), btn_down_pressed, FALLING );
  attachInterrupt(digitalPinToInterrupt(BTN_LEFT), btn_left_pressed, FALLING );
  attachInterrupt(digitalPinToInterrupt(BTN_RIGHT), btn_right_pressed, FALLING );

  pinMode(PIN_VOLTAGE,INPUT); //pin di ingresso della tensione del pannellino solare

  compass.init(); //Inizializzazione bussola

  /* Primo display del menu */
  SelezioneMenu(menu_hight_1,menu_dept,menu_hight_2,PIN_VOLTAGE,servo_controller.servoAz.get_alpha(),servo_controller.servoEl.get_alpha());

  /* Impostazione dello stato di partenza */
  current_state = STATE_ACTIONS;
}

void loop() {
  /* viene eseguita la funzione corrispondente al current state */
  fsm[current_state].state_function(); 

  /* aggiornamento del menu */
  SelezioneMenu(menu_hight_1,menu_dept,menu_hight_2,PIN_VOLTAGE,servo_controller.servoAz.get_alpha(),servo_controller.servoEl.get_alpha());
}

/*
Invio i messaggi di setup definiti in precedenze al ricevitore GNSS per sospendere la ricezione di tutti i messaggi ad eccezione dei GNRMC
ATTENZIONE: è fondamentale aspettare almeno 1000ms tra un invio e l'altro (come da HW Integration Manual) per assicurare
            la corretta ricezione dei messaggi
*/
void setupM8Q() {
  delay(2000);
  for(size_t i = 0; i < sizeof(UBX_CFG_MSG_GGA_OFF); ++i) {
    Serial2.write(UBX_CFG_MSG_GGA_OFF[i]);
  }
  // Debug
  Serial.println("Fatto GGA");
  delay(1000);

  for(size_t i = 0; i < sizeof(UBX_CFG_MSG_GSV_OFF); ++i) {
    Serial2.write(UBX_CFG_MSG_GSV_OFF[i]);
  }
  // Debug
  Serial.println("Fatto GSV");
  delay(1000);

  for(size_t i = 0; i < sizeof(UBX_CFG_MSG_GSA_OFF); ++i) {
    Serial2.write(UBX_CFG_MSG_GSA_OFF[i]);
  }
  // Debug
  Serial.println("Fatto GSA");
  delay(1000);

  for (size_t i = 0; i < sizeof(UBX_CFG_MSG_VTG_OFF); ++i) {
    Serial2.write(UBX_CFG_MSG_VTG_OFF[i]);
  }
  // Debug
  Serial.println("Fatto VTG");
  delay(1000);

  for (size_t i = 0; i < sizeof(UBX_CFG_MSG_GLL_OFF); ++i) {
    Serial2.write(UBX_CFG_MSG_GLL_OFF[i]);
  }
  // Debug
  Serial.println("Fatto GLL");
}


int pacMan(int start ,int val, int range){
  val = val>range ? start : val;
  val = val<start ? range : val;
  return val;
}

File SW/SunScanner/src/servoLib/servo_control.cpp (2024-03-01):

#include "servoLib/servo_control.h"

/* Costruttore */
ServoController::ServoController(int pin_az, int pin_el, int current_p, int voltage_p):
	servoAz(360,pin_az),
	servoEl(180,pin_el){
	current_pin = current_p;
	voltage_pin = voltage_p;
	pinMode(current_pin,INPUT);
	pinMode(voltage_pin,INPUT);
}

/* point to sun automatically */
void ServoController::auto_positioning(tm* time_info_ptr, double Lat, double Lon, double Alt, double compass_val, double* Az, double* El){
	int azpos;
	SolarAzEl(time_info_ptr, Lat, Lon, Alt, Az, El);
	azpos=*(Az);

	/* compass adjustments */
	if(compass_val>180){
		azpos+=(360-compass_val);
	}else{
		azpos-=compass_val;
	}
	
  	/* these adjustments work if the 0 angle of the servoAz face same direction of compass */
	servoAz.set_servo(azpos);
	servoEl.set_servo(*(El));
}

/* ADC read of voltage and current from solar panel */
double ServoController::get_voltage(){
	int voltage = analogRead(voltage_pin);
	return(voltage);
}

/* Function that point at the most power efficient point  */
/* step => how many degrees each servo move per iteration */
/* n_iter => how many step are taken in each direction */
void ServoController::max_power_pos(double step, int n_iter){
	int pow, max_pow_az, max_pow_el;
	int i;
	double max_az, max_el; 
	double initial_el = servoEl.get_alpha();  //starting angle of elevation servo
	double initial_az = servoAz.get_alpha();  //starting angle of azimuth servo

	max_az = initial_az;
	max_el = initial_el;
	max_pow_az = max_pow_el = get_voltage()*get_current();
	for(i=0;i<n_iter;++i){
		double az = servoAz.get_alpha();
		servoAz.set_servo(az-step);  //moving servo of step degree
		pow=get_voltage()*get_current();  //calculating power
		if(pow>max_pow_az){  //finding the most powerful position
			max_pow_az = pow;
			max_az = az-step;
		}
	}
	
	servoAz.set_servo(initial_az);
	for(i=0;i<n_iter;++i){
		double az = servoAz.get_alpha();
		servoAz.set_servo(az+step); 
		pow=get_voltage()*get_current();
		if(pow>max_pow_az){
			max_pow_az = pow;
			max_az = az+step;
		}
	}
	
	servoAz.set_servo(initial_az);
	for(i=0;i<n_iter;++i){
		double el = servoEl.get_alpha();
		servoEl.set_servo(el+step);
		pow=get_voltage()*get_current();
		if(pow>max_pow_el){
			max_pow_el = pow;
			max_el = el+step;
		}
	}
	
	servoEl.set_servo(initial_el);
	for(i=0;i<n_iter;++i){
		double el = servoEl.get_alpha();
		servoEl.set_servo(el-step);
		pow=get_voltage()*get_current();
		if(pow>max_pow_el){
			max_pow_el = pow;
			max_el = el-step;
		}
	}
	delay(500);
	
	servoAz.set_servo(max_az);
	servoEl.set_servo(max_el);
}

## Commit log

2024-02-27 Added buck enable
2024-02-27 prove led
2024-02-29 commentato il main più piccoli cambiamenti
2024-03-12 Added SW and DOCS folders
    [involucro_misure.dxf]
2024-03-12 added 3D models
    [asse_primario.stl, base.stl, braccio.stl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]
